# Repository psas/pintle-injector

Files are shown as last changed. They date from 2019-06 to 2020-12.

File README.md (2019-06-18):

# Background

The Portland State Aerospace Society (PSAS) is seeking to launch a liquid bi-propellant rocket to a height of 100 km. One of the principal challenges in this endeavor is the development and testing of the rocket engine and associated subsystems. 

PSAS chose to develop a smaller scale, 2.2kN test engine prior to attempting a 100 km capable design. This is in keeping with PSAS’s technology development philosophy of iterative design where initial designs are built, tested, broken, and iterated towards fully functional and flight ready designs. 

The 2.2kN engine was designed to employ a liquid oxygen (LOX) centered pintle. In this design, LOX flows through the center of the pintle and is sprayed outward in a radial pattern. The fuel enters a chamber surrounding the base of the pintle and flows into the engine through the annular gap between the outer diameter of the pintle and the engine. (See Figures 1 & 2) Inside of the combustion chamber, the two propellants impinge upon each other at right angles. This, ideally, results in a cone shaped spray of well mixed fuel and oxidizer. 
 
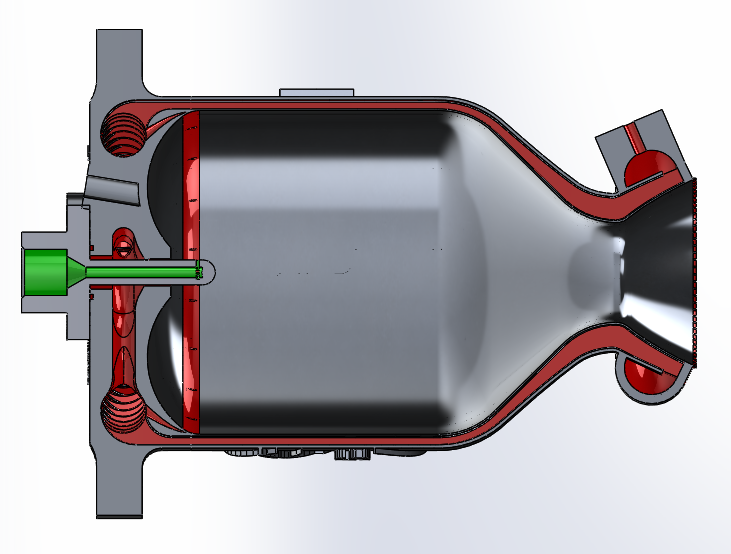
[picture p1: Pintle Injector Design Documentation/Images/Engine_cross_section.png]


>Figure 1: Cross section of 2.2 kN engine. Fuel flow path shown in red, LOX flow path shown in green.

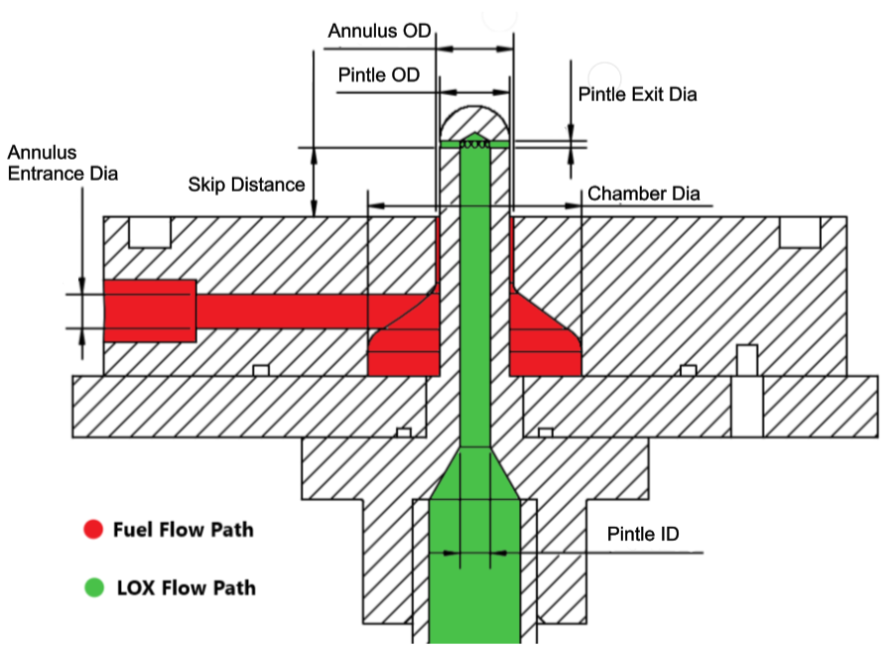
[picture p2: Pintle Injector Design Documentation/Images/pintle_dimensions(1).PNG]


> Figure 2: cross section view of genaric pintle V1 & V2 geometry.

The choice to use this style of injector was finalized by the 2015-2016 capstone team who designed the 2.2kN engine. The use of a pintle type injector is not specifically required for this size of engine. That stated, the initial 2.2kN engine was designed specifically to work with a pintle type injector, which locked a number of the design parameters which may have otherwise been available. The most noteworthy restrictions imposed are that the injector can only be LOX centered, and has a maximum envelope for the outer diameter of the annular gap.

# Theory and Design 

An instructional document was created while developing the injector for our first engine that attempts to distill the fundamental theory, design parameters, and the lessons learned from this project.

# V Series Injector

The first pintle injector design developed is the V series.

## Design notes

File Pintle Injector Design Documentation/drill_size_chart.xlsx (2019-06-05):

Size | Decimal Equivalent (in)
97 | 0.0059
96 | 0.0063
95 | 0.0067
94 | 0.0071
93 | 0.0075
92 | 0.0079
91 | 0.0083
90 | 0.0087
89 | 0.0091
88 | 0.0095
.25 mm | 0.0098
87 | 0.01
86 | 0.0105
85 | 0.011
84 | 0.0115
.30 mm | 0.0118
83 | 0.012
82 | 0.0125
.32 mm | 0.0126
81 | 0.013
80 | 0.0135
.35 mm | 0.0138
.36 mm | 0.0142
79 | 0.0145
.38 mm | 0.015
1/64" | 0.0156
.40 mm | 0.0157
78 | 0.016
.42 mm | 0.0165
.44 mm | 0.0173
.45 mm | 0.0177
77 | 0.018
.46 mm | 0.0181
.48 mm | 0.0189
.50 mm | 0.0197
76 | 0.02
75 | 0.021
.55 mm | 0.0217
74 | 0.0225
.60 mm | 0.0236
73 | 0.024
72 | 0.025
.65 mm | 0.0256
71 | 0.026
.70 mm | 0.0276
70 | 0.028
69 | 0.0292
.75 mm | 0.0295
68 | 0.031
1/32" | 0.0312
.80 mm | 0.0315
67 | 0.032
66 | 0.033
.85 mm | 0.0335
65 | 0.035
.90 mm | 0.0354
64 | 0.036
63 | 0.037
.95 mm | 0.0374
62 | 0.038
61 | 0.039
1.00 mm | 0.0394
60 | 0.04
59 | 0.041
1.05 mm | 0.0413
58 | 0.042
57 | 0.043
1.10 mm | 0.0433
1.15 mm | 0.0453
56 | 0.0465
3/64" | 0.0469
1.20 mm | 0.0472
1.25 mm | 0.0492
1.30 mm | 0.0512
55 | 0.052
1.35 mm | 0.0531
54 | 0.055
1.40 mm | 0.0551
1.45 mm | 0.0571
1.50 mm | 0.0591
53 | 0.0595
1.55 mm | 0.061
1/16" | 0.0625
1.60 mm | 0.063
52 | 0.0635
1.65 mm | 0.065
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

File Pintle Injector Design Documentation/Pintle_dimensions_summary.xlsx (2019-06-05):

Pintle Injector V1 |  |  | Pintle Injector V2
Pintle |  |  | Pintle
Flow Entrance dia. | 0.402 | in | Flow Entrance dia. | 0.402 | in
Inner Diameter | 0.12 | in | Inner Diameter | 0.221 | in
Orifice diameter | 0.03125 | in | Orifice diameter | 0.0595 | in
# of orifices | 12 | - | # of orifices | 12 | -
Wall Thickness | 0.0805 | in | Wall Thickness | 0.1 | in
Blockage Factor | 0.425 | - | Blockage Factor | 0.540 | -
Annulus |  |  | Annulus
Flow Entrance dia. | 0.136 | in | Flow Entrance dia. | 0.25 | in
# of Entrances | 1 | - | # of Entrances | 1 | -
Chamber radius | 0.4325 | in | Chamber radius | 0.4325 | in
Pintle OD | 0.281 | in | Pintle OD | 0.421 | in
Annulus Outer dia. | 0.3105 | in | Annulus Outer dia. | 0.4688 | in
Annular Gap | 0.01475 | in | Annular Gap | 0.0239 | in

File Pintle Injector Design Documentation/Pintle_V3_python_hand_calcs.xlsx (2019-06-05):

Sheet: Injector V3 mjp T4A
Pintle |  | values | units |  | Annulus |  | values | units
Entrance diameter |  | 0.44 | in |  | Entrance diameter |  | 0.25 | in
Inner Diameter |  | 0.221 | in |  | Channel Width |  | 0.25 | in
Outer Diameter |  | 0.421 | in |  | Channel Depth |  | 0.21 | in
Exit Diameter |  | 0.0635 | in |  | Chamber Diameter |  | 0.865 | in
Number of Orifices |  | 12 |  |  | Annulus Outer Diameter |  | 0.5156 | in
Blockage Factor |  | 0.576 |  |  | Annular Gap |  | 0.0473 | in
Pintle Version | Estimated Loss coef | Working Fluid | T intensity | T lenght Scale mm
MJP test 4 | 2.967 | water | 0.1225 | 4.247
Pintle Hand Calculations |  |  |  |  |  |  |  |  |  |  |  | Pintle CFD Results |  |  |  |  |  |  |  |  |  | Experimental Results
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

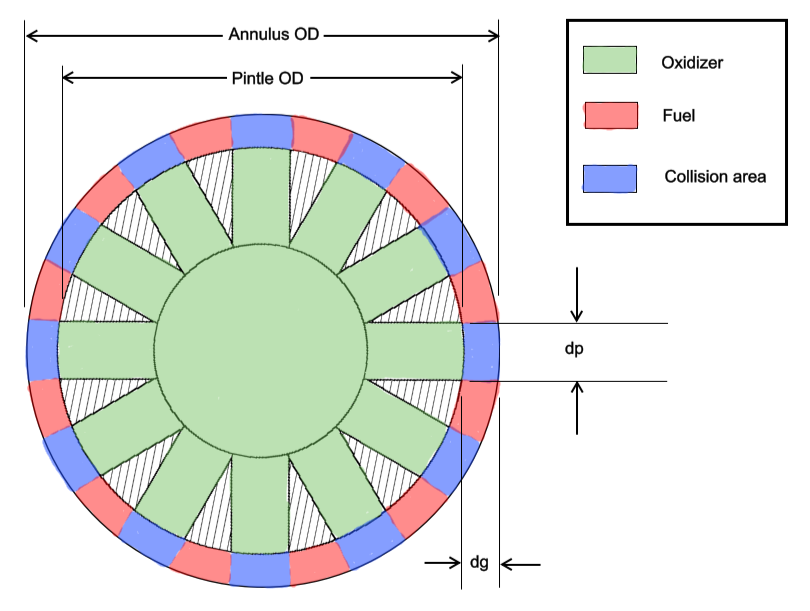
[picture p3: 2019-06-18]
Pintle Injector Design Documentation/Images/momentum_ratio_diagram.PNG

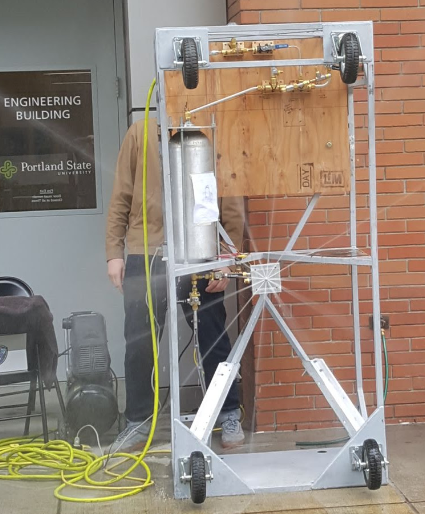
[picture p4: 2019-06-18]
Pintle Injector Design Documentation/Images/V2_radial_spray2.PNG

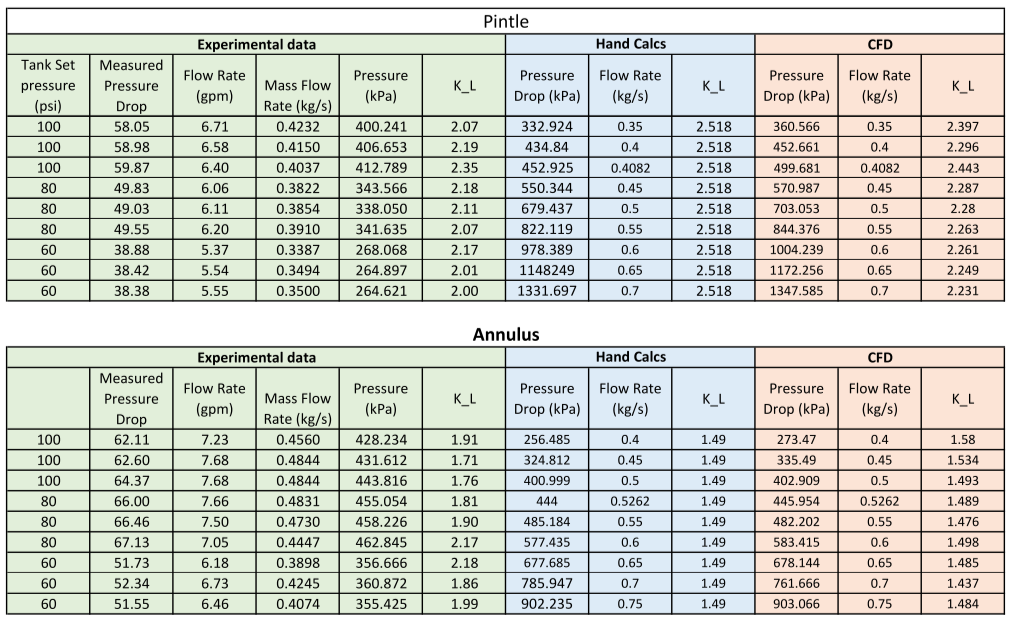
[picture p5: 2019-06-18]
Pintle Injector Design Documentation/Images/V2_data_summary.PNG

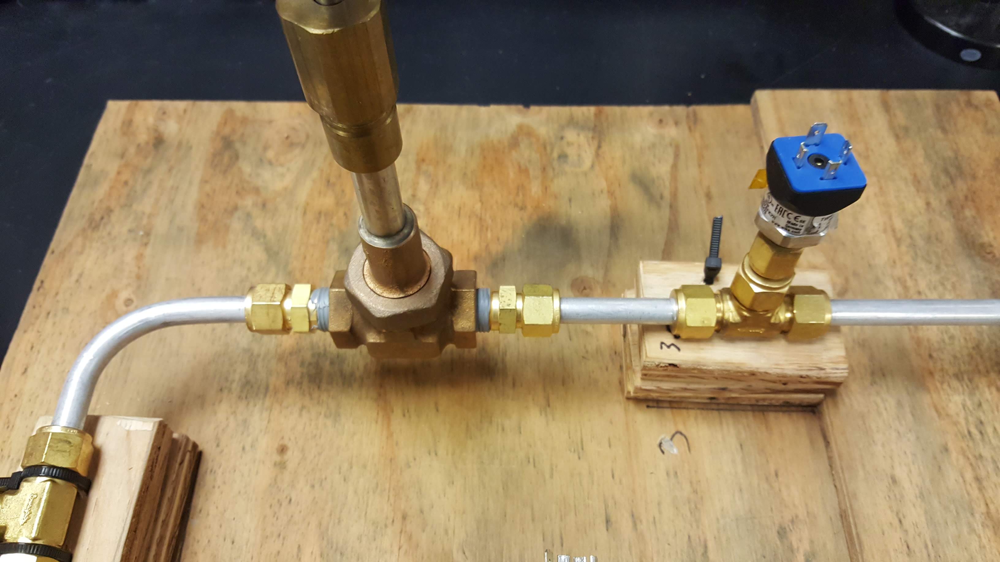
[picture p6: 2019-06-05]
Pintle Injector Design Documentation/Images/globe valve set up.jpg

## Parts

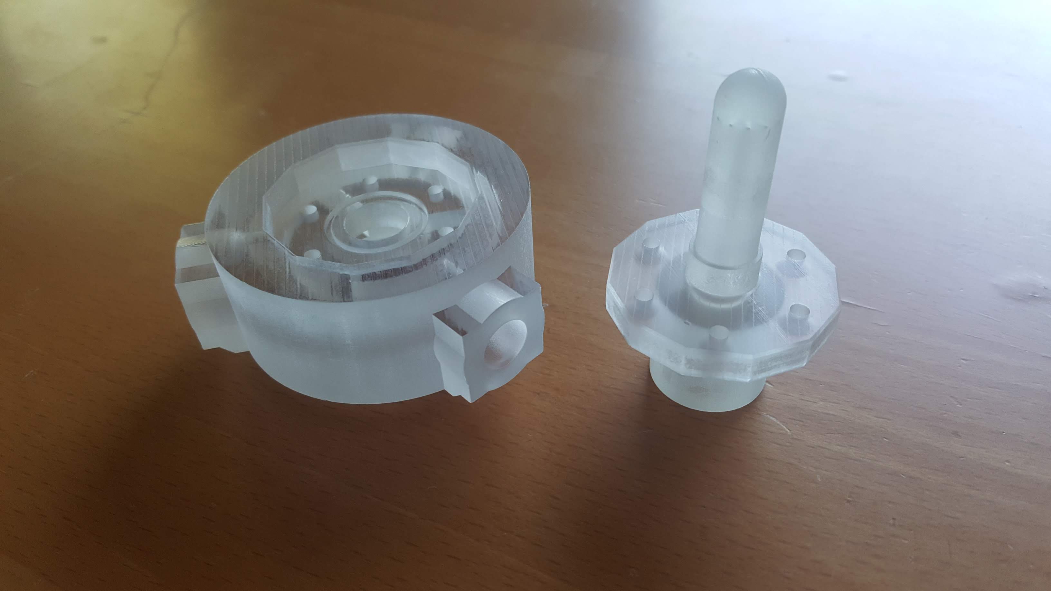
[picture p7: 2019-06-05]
V_Series/Images/V3_injector_parts.jpg

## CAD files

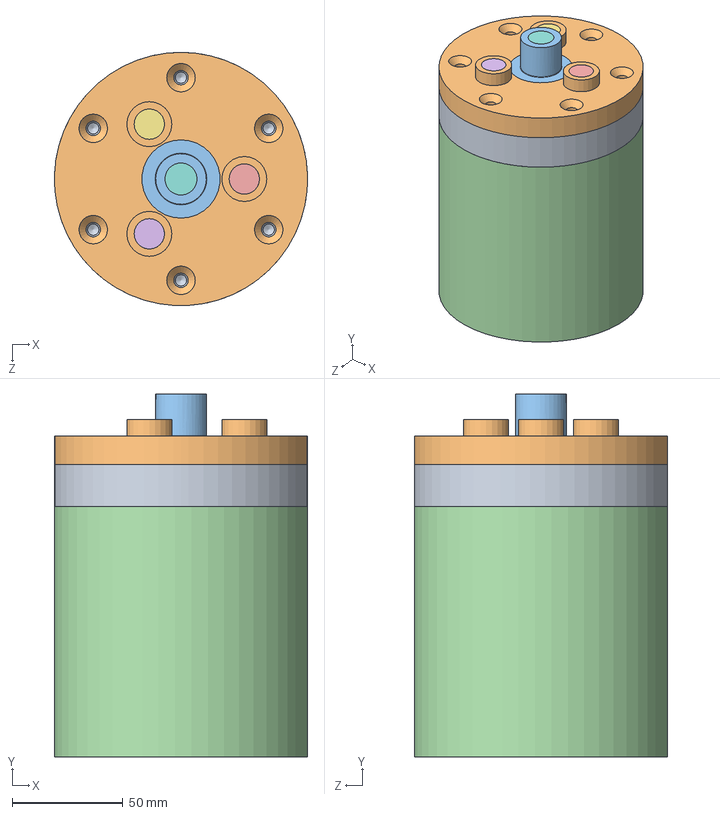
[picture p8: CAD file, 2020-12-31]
V_Series/Pintle_V3_CAD/Assembly_Pintle_V3.SLDASM
114.2 x 163.8 x 114.3 mm
Part_annulus_base_v3
Part_V3_Top_Plate
Part_V3_Pintle
Outlet_Lid_For_Sim
LID1
LID2
LID3
LID4

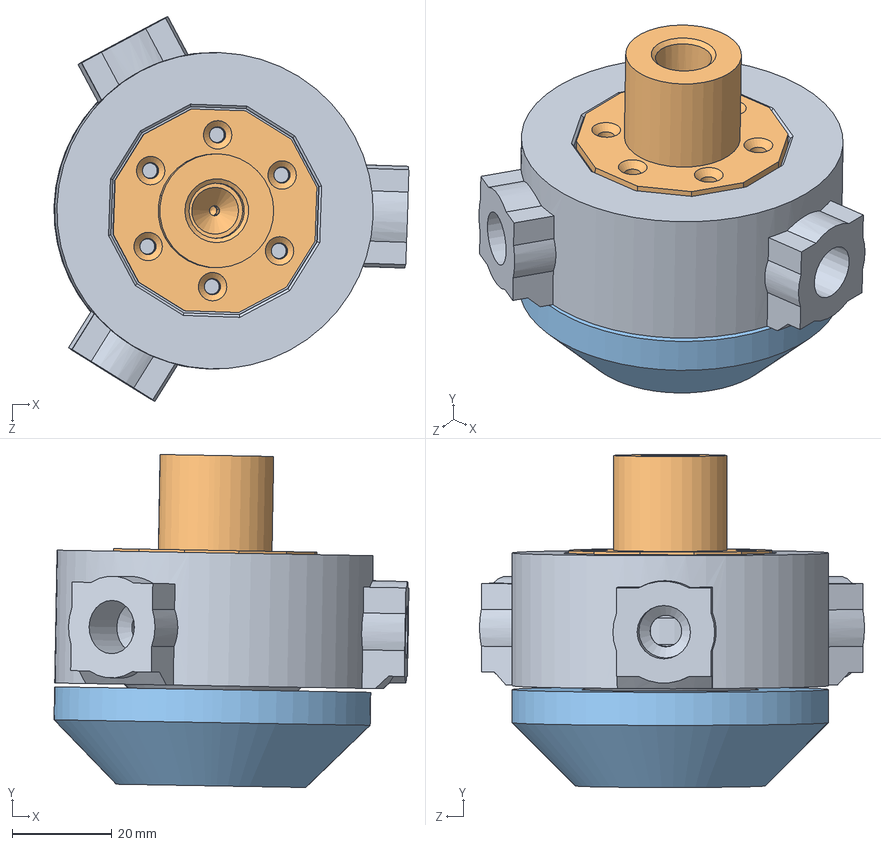
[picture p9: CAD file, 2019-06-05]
V_Series/Pintle_V3_CAD/Assembly_Pintle_V3_MJP.SLDASM
71.2 x 66.8 x 77.3 mm
Part_annulus_base_v3_mjp
Part_V3_Pintle_MJP
Part_mjp_support

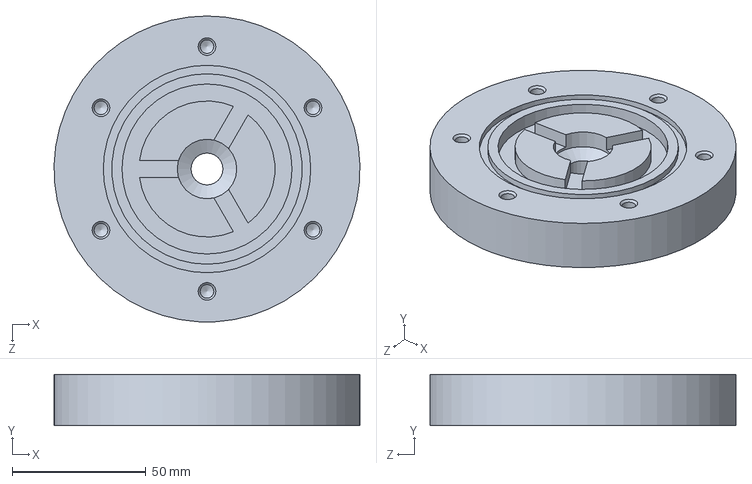
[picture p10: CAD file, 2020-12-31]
V_Series/Pintle_V3_CAD/Part_annulus_base_v3.SLDPRT
114.2 x 19.1 x 114.3 mm

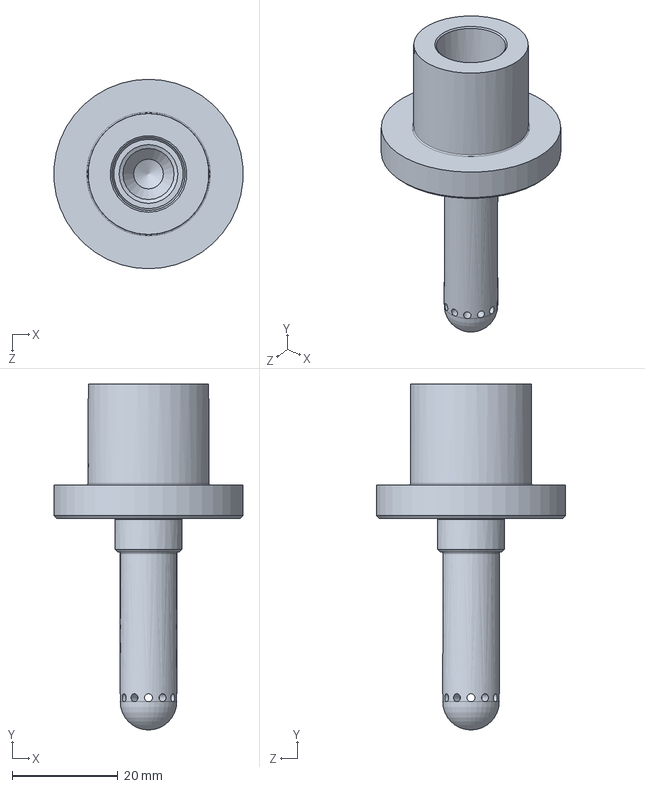
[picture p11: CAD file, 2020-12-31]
V_Series/Pintle_V3_CAD/Part_V3_Pintle.SLDPRT
35.7 x 65.4 x 35.8 mm

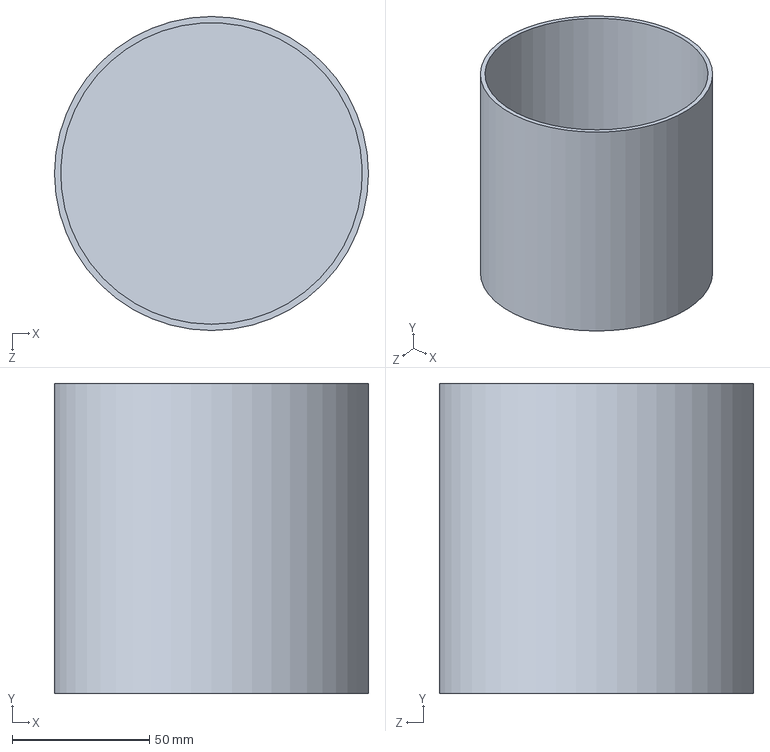
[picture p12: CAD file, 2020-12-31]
V_Series/Pintle_V3_CAD/Outlet_Lid_For_Sim.SLDPRT
114.3 x 113.0 x 114.3 mm

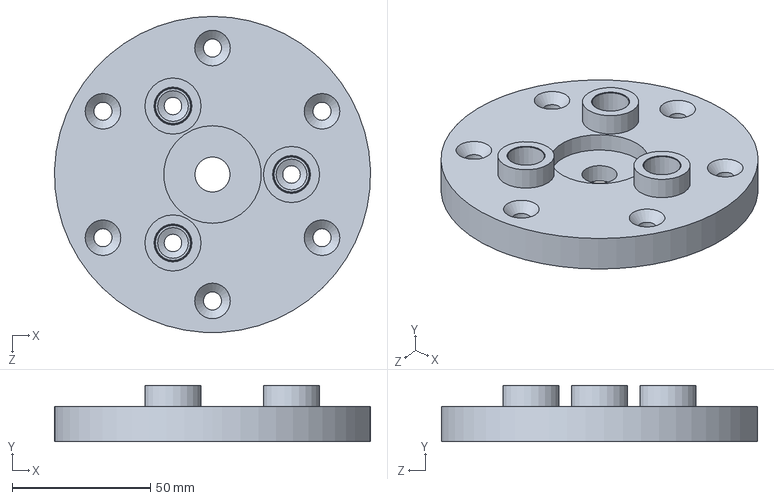
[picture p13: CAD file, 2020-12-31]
V_Series/Pintle_V3_CAD/Part_V3_Top_Plate.SLDPRT
114.2 x 20.3 x 114.3 mm

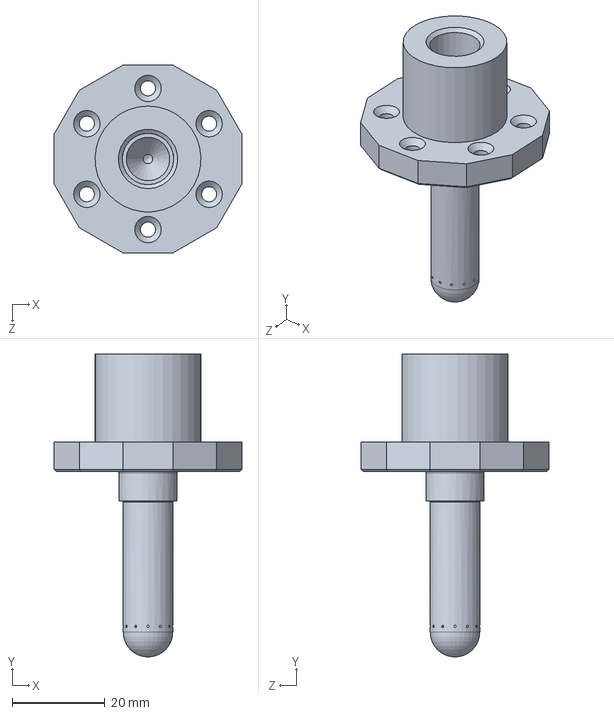
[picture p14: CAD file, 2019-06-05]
V_Series/Pintle_V3_CAD/Part_V3_Pintle_MJP.SLDPRT
40.5 x 65.4 x 40.5 mm

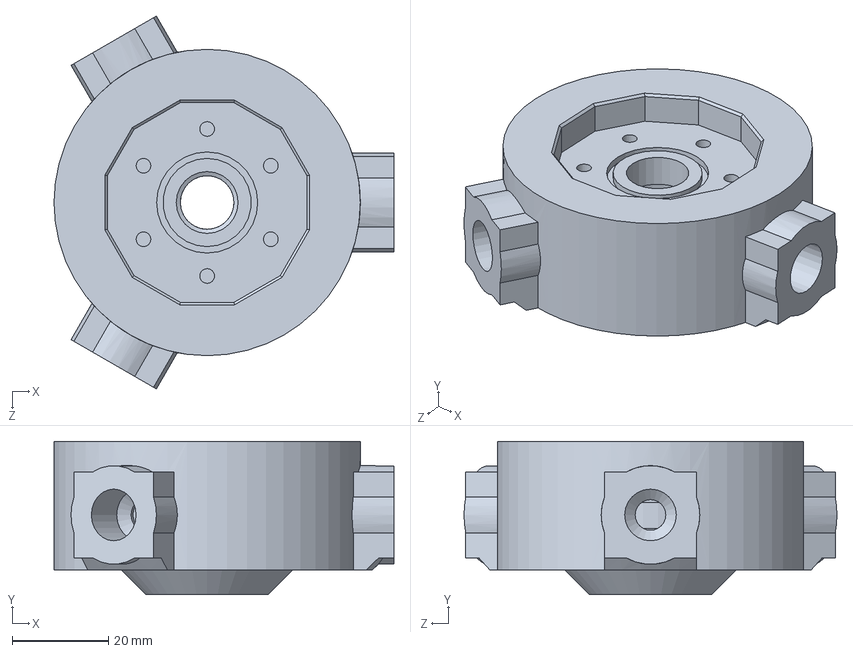
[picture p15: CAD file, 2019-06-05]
V_Series/Pintle_V3_CAD/Part_annulus_base_v3_mjp.SLDPRT
70.5 x 31.8 x 77.3 mm

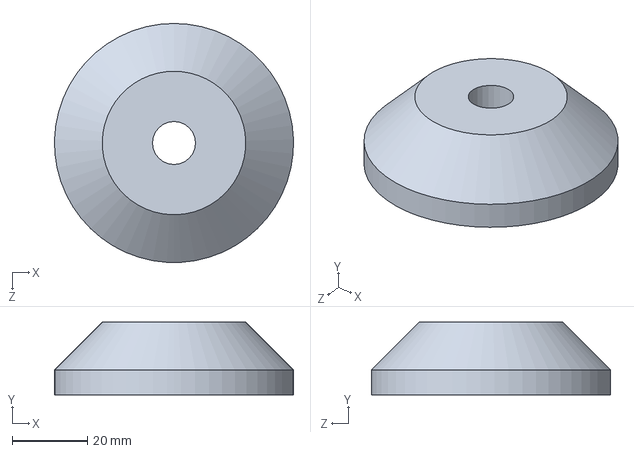
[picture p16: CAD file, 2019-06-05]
V_Series/Pintle_V3_CAD/Part_mjp_support.SLDPRT
63.5 x 19.3 x 63.5 mm

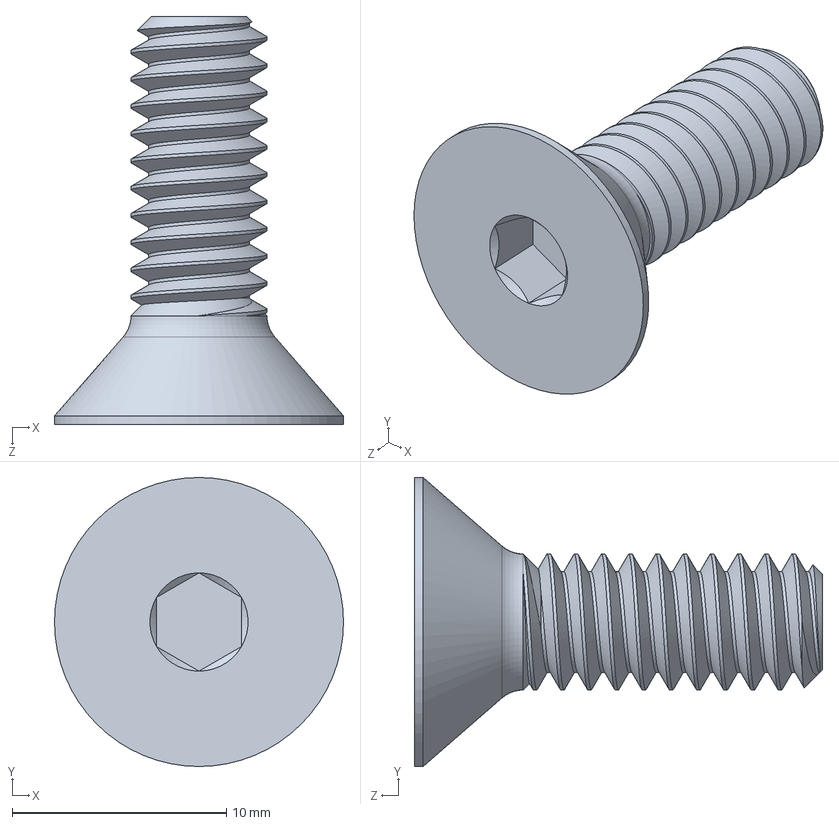
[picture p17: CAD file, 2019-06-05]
V_Series/Pintle_V3_CAD/90585A540_TYPE 316 SS FLAT-HEAD SOCKET CAP SCREW.SLDPRT
13.5 x 13.5 x 19.1 mm

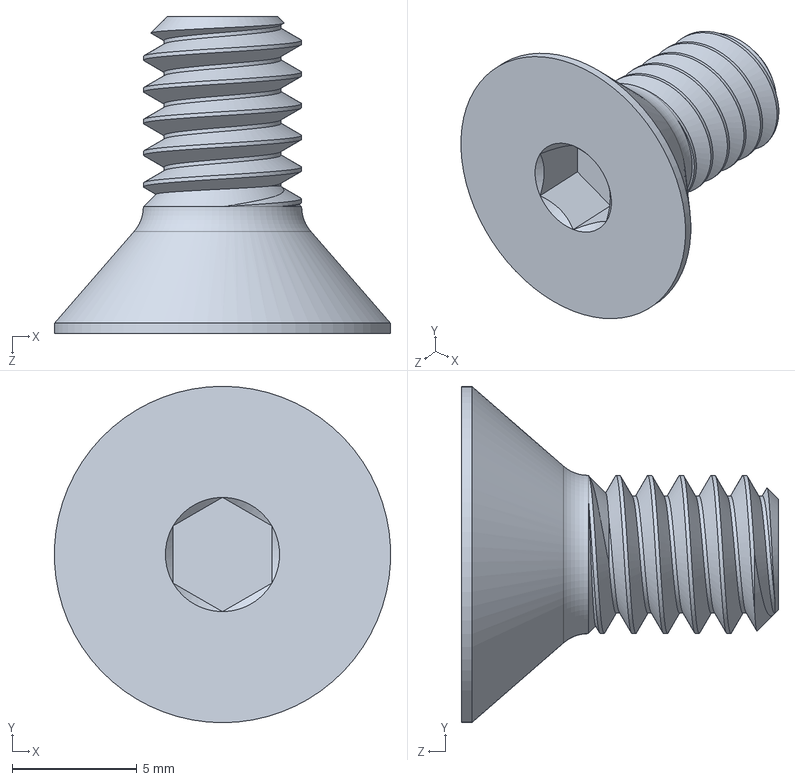
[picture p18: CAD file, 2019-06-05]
V_Series/Pintle_V3_CAD/90585A537_TYPE 316 SS FLAT-HEAD SOCKET CAP SCREW (1).SLDPRT
13.5 x 13.5 x 12.7 mm

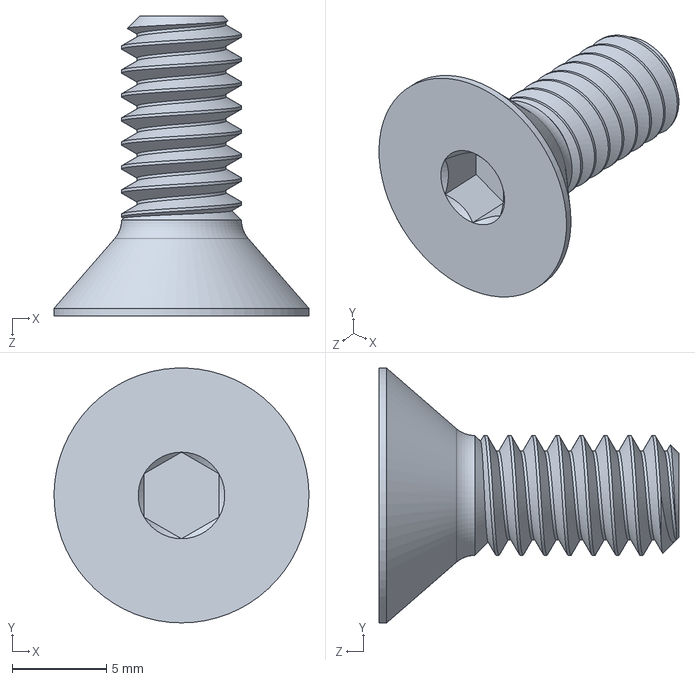
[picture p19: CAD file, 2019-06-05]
V_Series/Pintle_V3_CAD/90585A358_TYPE 316 SS FLAT-HEAD SOCKET CAP SCREW.SLDPRT
13.5 x 13.5 x 15.9 mm

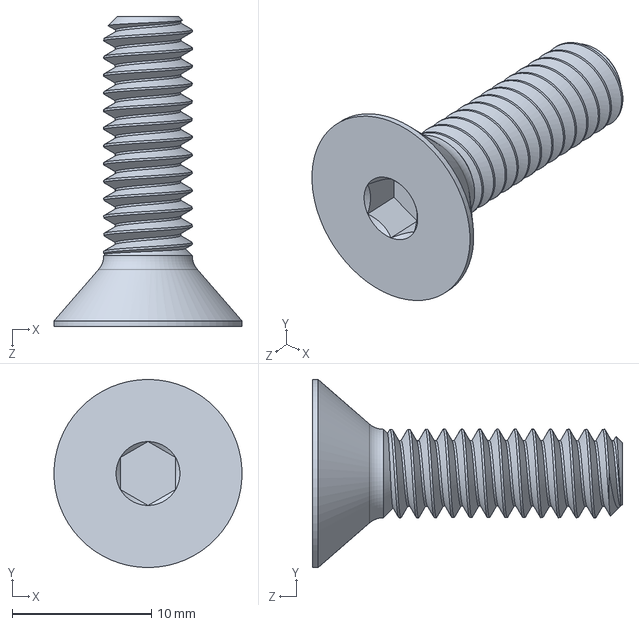
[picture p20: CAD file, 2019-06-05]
V_Series/Pintle_V3_CAD/90585A541_TYPE 316 SS FLAT-HEAD SOCKET CAP SCREW.SLDPRT
13.5 x 13.5 x 22.2 mm

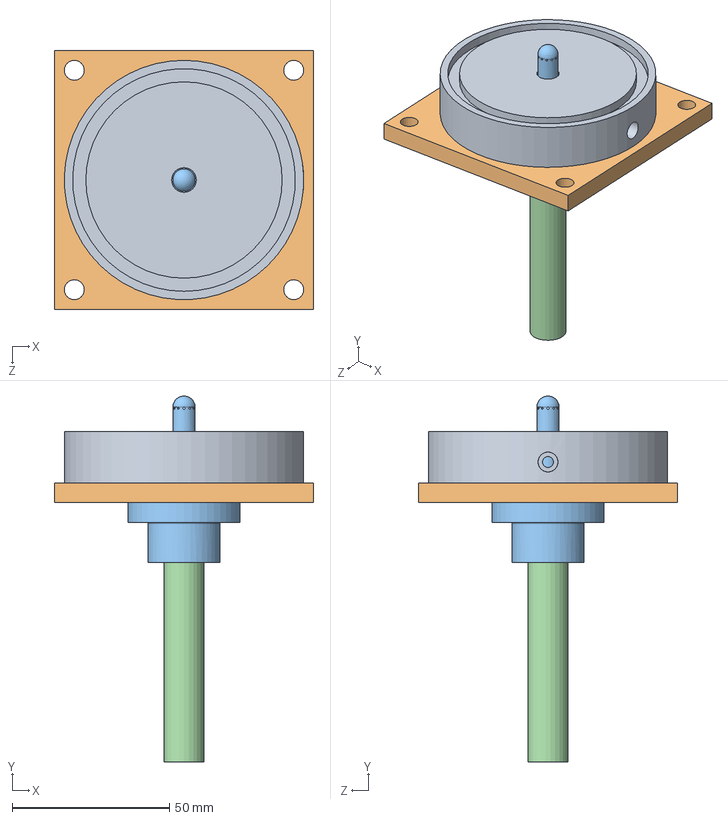
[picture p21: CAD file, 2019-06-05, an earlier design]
V_Series/Pintle_V1_CAD/Assembly_Cold_Test.SLDASM
82.5 x 116.5 x 82.5 mm
Part_Cold_Test_Annulus_V1
Part_Cold_Test_Plate_V1
Part_Pintle_V1
Part_SSTube

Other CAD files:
V_Series/Pintle_V3_CAD/LID1.SLDPRT
V_Series/Pintle_V3_CAD/LID4.SLDPRT
V_Series/Pintle_V3_CAD/LID2.SLDPRT
V_Series/Pintle_V3_CAD/LID3.SLDPRT
V_Series/Pintle_V1_CAD/Assembly_Cold_Test dimensions.SLDDRW
V_Series/Pintle_V1_CAD/Part_Cold_Test_Annulus_V1.SLDPRT
V_Series/Pintle_V1_CAD/Part_Cold_Test_Plate_V1.SLDPRT
V_Series/Pintle_V1_CAD/Part_Pintle_V1.SLDPRT
V_Series/Pintle_V1_CAD/Part_Pintle_V2.2.SLDPRT
V_Series/Pintle_V1_CAD/Part_SSTube.SLDPRT
V_Series/Pintle_V1_CAD/test.SLDASM
V_Series/Pintle_V2_CAD/Assembly_Jig_V2.SLDASM
V_Series/Pintle_V2_CAD/Assembly_V2_Cold_Test.SLDASM
V_Series/Pintle_V2_CAD/Drawing_V2_Cold_Test_Annulus_rough.SLDDRW
V_Series/Pintle_V2_CAD/Drawing_V2_Cold_Test_Plate_rough.SLDDRW
V_Series/Pintle_V2_CAD/Drawing_V2_Pintle_rough.SLDDRW
V_Series/Pintle_V2_CAD/Part_SSTube.SLDPRT
V_Series/Pintle_V2_CAD/Part_V1_Pintle.SLDPRT
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

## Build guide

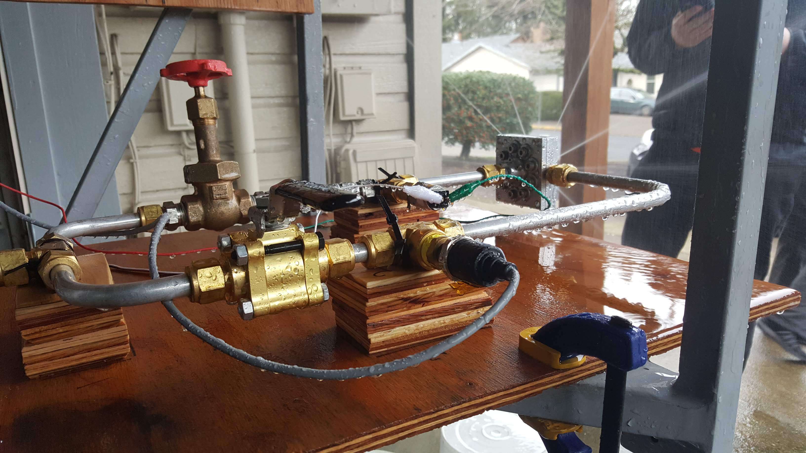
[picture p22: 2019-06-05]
V_Series/Images/Initial setup.jpg

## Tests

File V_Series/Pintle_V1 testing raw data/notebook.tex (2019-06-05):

% Default to the notebook output style

% Inherit from the specified cell style.

\documentclass[11pt]{article}

    \usepackage[T1]{fontenc}
    % Nicer default font (+ math font) than Computer Modern for most use cases
    \usepackage{mathpazo}

    % Basic figure setup, for now with no caption control since it's done
    % automatically by Pandoc (which extracts ![](path) syntax from Markdown).
    \usepackage{graphicx}
    % We will generate all images so they have a width \maxwidth. This means
    % that they will get their normal width if they fit onto the page, but
    % are scaled down if they would overflow the margins.
    \makeatletter
    \def\maxwidth{\ifdim\Gin@nat@width>\linewidth\linewidth
    \else\Gin@nat@width\fi}
    \makeatother
    \let\Oldincludegraphics\includegraphics
    % Set max figure width to be 80% of text width, for now hardcoded.
    \renewcommand{\includegraphics}[1]{\Oldincludegraphics[width=.8\maxwidth]{#1}}
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
\expandafter\def\csname PY@tok@kc\endcsname{\let\PY@bf=\textbf\def\PY@tc##1{\textcolor[rgb]{0.00,0.50,0.00}{##1}}}
\expandafter\def\csname PY@tok@kd\endcsname{\let\PY@bf=\textbf\def\PY@tc##1{\textcolor[rgb]{0.00,0.50,0.00}{##1}}}
\expandafter\def\csname PY@tok@kn\endcsname{\let\PY@bf=\textbf\def\PY@tc##1{\textcolor[rgb]{0.00,0.50,0.00}{##1}}}
\expandafter\def\csname PY@tok@kr\endcsname{\let\PY@bf=\textbf\def\PY@tc##1{\textcolor[rgb]{0.00,0.50,0.00}{##1}}}
\expandafter\def\csname PY@tok@bp\endcsname{\def\PY@tc##1{\textcolor[rgb]{0.00,0.50,0.00}{##1}}}
\expandafter\def\csname PY@tok@fm\endcsname{\def\PY@tc##1{\textcolor[rgb]{0.00,0.00,1.00}{##1}}}
\expandafter\def\csname PY@tok@vc\endcsname{\def\PY@tc##1{\textcolor[rgb]{0.10,0.09,0.49}{##1}}}
\expandafter\def\csname PY@tok@vg\endcsname{\def\PY@tc##1{\textcolor[rgb]{0.10,0.09,0.49}{##1}}}
\expandafter\def\csname PY@tok@vi\endcsname{\def\PY@tc##1{\textcolor[rgb]{0.10,0.09,0.49}{##1}}}
\expandafter\def\csname PY@tok@vm\endcsname{\def\PY@tc##1{\textcolor[rgb]{0.10,0.09,0.49}{##1}}}
\expandafter\def\csname PY@tok@sa\endcsname{\def\PY@tc##1{\textcolor[rgb]{0.73,0.13,0.13}{##1}}}
\expandafter\def\csname PY@tok@sb\endcsname{\def\PY@tc##1{\textcolor[rgb]{0.73,0.13,0.13}{##1}}}
\expandafter\def\csname PY@tok@sc\endcsname{\def\PY@tc##1{\textcolor[rgb]{0.73,0.13,0.13}{##1}}}
\expandafter\def\csname PY@tok@dl\endcsname{\def\PY@tc##1{\textcolor[rgb]{0.73,0.13,0.13}{##1}}}
\expandafter\def\csname PY@tok@s2\endcsname{\def\PY@tc##1{\textcolor[rgb]{0.73,0.13,0.13}{##1}}}
\expandafter\def\csname PY@tok@sh\endcsname{\def\PY@tc##1{\textcolor[rgb]{0.73,0.13,0.13}{##1}}}
\expandafter\def\csname PY@tok@s1\endcsname{\def\PY@tc##1{\textcolor[rgb]{0.73,0.13,0.13}{##1}}}
\expandafter\def\csname PY@tok@mb\endcsname{\def\PY@tc##1{\textcolor[rgb]{0.40,0.40,0.40}{##1}}}
\expandafter\def\csname PY@tok@mf\endcsname{\def\PY@tc##1{\textcolor[rgb]{0.40,0.40,0.40}{##1}}}
\expandafter\def\csname PY@tok@mh\endcsname{\def\PY@tc##1{\textcolor[rgb]{0.40,0.40,0.40}{##1}}}
\expandafter\def\csname PY@tok@mi\endcsname{\def\PY@tc##1{\textcolor[rgb]{0.40,0.40,0.40}{##1}}}
\expandafter\def\csname PY@tok@il\endcsname{\def\PY@tc##1{\textcolor[rgb]{0.40,0.40,0.40}{##1}}}
\expandafter\def\csname PY@tok@mo\endcsname{\def\PY@tc##1{\textcolor[rgb]{0.40,0.40,0.40}{##1}}}
\expandafter\def\csname PY@tok@ch\endcsname{\let\PY@it=\textit\def\PY@tc##1{\textcolor[rgb]{0.25,0.50,0.50}{##1}}}
\expandafter\def\csname PY@tok@cm\endcsname{\let\PY@it=\textit\def\PY@tc##1{\textcolor[rgb]{0.25,0.50,0.50}{##1}}}
\expandafter\def\csname PY@tok@cpf\endcsname{\let\PY@it=\textit\def\PY@tc##1{\textcolor[rgb]{0.25,0.50,0.50}{##1}}}
\expandafter\def\csname PY@tok@c1\endcsname{\let\PY@it=\textit\def\PY@tc##1{\textcolor[rgb]{0.25,0.50,0.50}{##1}}}
\expandafter\def\csname PY@tok@cs\endcsname{\let\PY@it=\textit\def\PY@tc##1{\textcolor[rgb]{0.25,0.50,0.50}{##1}}}

\def\PYZbs{\char`\\}
\def\PYZus{\char`\_}
\def\PYZob{\char`\{}
\def\PYZcb{\char`\}}
\def\PYZca{\char`\^}
\def\PYZam{\char`\&}
\def\PYZlt{\char`\<}
\def\PYZgt{\char`\>}
\def\PYZsh{\char`\#}
\def\PYZpc{\char`\%}
\def\PYZdl{\char`\$}
\def\PYZhy{\char`\-}
\def\PYZsq{\char`\'}
\def\PYZdq{\char`\"}
\def\PYZti{\char`\~}
% for compatibility with earlier versions
\def\PYZat{@}
\def\PYZlb{[}
\def\PYZrb{]}
\makeatother

    % Exact colors from NB
    \definecolor{incolor}{rgb}{0.0, 0.0, 0.5}
    \definecolor{outcolor}{rgb}{0.545, 0.0, 0.0}

    % Prevent overflowing lines due to hard-to-break entities
    \sloppy 
    % Setup hyperref package
    \hypersetup{
      breaklinks=true,  % so long urls are correctly broken across lines
      colorlinks=true,
      urlcolor=urlcolor,
      linkcolor=linkcolor,
      citecolor=citecolor,
      }
    % Slightly bigger margins than the latex defaults
    
    \geometry{verbose,tmargin=1in,bmargin=1in,lmargin=1in,rmargin=1in}

    \begin{document}

    \maketitle

    \section{Pintle V1 Test for 2.2kN Liquid Propellant Rocket
Engine}\label{pintle-v1-test-for-2.2kn-liquid-propellant-rocket-engine}

Dates of testing: 1/19/19, 1/26/19 \& 2/3/19

    \section{Introduction}\label{introduction}

The Portland State Aerospace Society is in the process of testing its
\(2.2kN\) (\(500 lb_f\)) regeneratively cooled bi-propellant rocket
motor. One of the critical steps prior to hot firing the motor is the
testing and validating of the propellant injector. For this motor, a
pintle style injector was selected and an aluminum test article was
machined according to the designs provided by the 2015 Capstone team.

    \section{Pintle Design:}\label{pintle-design}

The engine was designed to employ a liquid oxygen (LOX) centered pintle
design. In this design, LOX flows throu the center of the pintle and is
sprayed outward in a radial pattern. The fuel enters a chamber
surrounding the base of the pintle and enters the engine through the
annular gap between the outer radius of the pintle and the engine. (See
Figures 1 \& 2) Inside of the combustion chamber, the two propellants
impinge upon eachother at right angles. This, ideally, results in a cone
shaped spray of well mixed fuel and oxidizer.

\begin{quote}
Figure 1: Cross section of 2.2 kN engine. Fuel flow path shown in red,
LOX flow path shown in green.
\end{quote}

\begin{quote}
Figure 2: Cross section of Pintle with basic dimensions for flow paths.
\end{quote}

\subsection{Relevant Design
Requirements:}\label{relevant-design-requirements}

The pintle injector needs to meet the following requirements:

\begin{enumerate}
\def\labelenumi{\arabic{enumi}.}
\tightlist
\item
  Oxidizer: Liquid Oxygen (LOX)
\item
  Fuel: 70\% Isoproply Alchohol (IPA), 30\% water
\item
  Meet mass flow rates at a pressure differential between 15-20 \% of
  chamber pressure:

  \begin{itemize}
  \tightlist
  \item
    Engine chamber pressure 350 psi (as designed)
  \item
    Target pressure differential: 53-70 psi\\
  \end{itemize}
\item
  LOX mass flow rate of 0.9 lbm/s (0.4082 kg/s)
\item
  Fuel mass flow rate of 1.16 lbm/s (0.5262 kg/s)
\end{enumerate}

    \section{Objectives}\label{objectives}

Desired data and outcomes:

\begin{itemize}
\tightlist
\item
  Determine loss coefficients (\(C_L\))

  \begin{itemize}
  \tightlist
  \item
    Pintle (LOX path)
  \item
    Annulus (Fuel path)
  \end{itemize}
\item
  Verify desired flow rates acheived at a delta pressure of 70 psi
\end{itemize}

    \section{Equations and Theory}\label{equations-and-theory}

The first testing objective was to determine the loss coefficients for
the Pintle and Annulus flow paths. For practical, cost, and safety
reasons the initial testing was performed using water.

Flow coefficient for the style of orifice plate used in testing {[}1{]};

\begin{equation}
C_v = \frac{Q_{gpm}}{\sqrt{\Delta P}}
\label{eq1}
\tag{1}
\end{equation}

Where;

\$C\_v = \$ the flow coefficient

\(Q_{gpm} =\) is the volumentric flow rate in gallons per minute

\$\Delta P = \$ is the difference in pressure across the orifice

\$ \textbackslash{} \$

Mass flow rate:

\begin{equation}
 \dot{m} = \rho VA
\label{eq2}
\tag{2}
\end{equation}

Energy Equation, with elevation, velocity, and head loss due to friction
neglected:

\begin{equation}
P_1  = P_2 + C_L\frac{\rho V_2^2}{2}
\label{eq3}
\tag{3}
\end{equation}

Combining equation \ref{eq2} and \ref{eq3} by substituting
\(V = \frac{\dot{m}}{\rho A}\) and rearranging gives

\begin{equation}
\dot{m} = C_LA \sqrt{2\rho(\Delta P)}
\label{eq4}
\tag{4}
\end{equation}

Where;

\$C\_L = \$ Loss coefficients for Pintle and Annulus: (to be calculated)

\(A =\) Flow area(s) of Pintle/Annulus

\(\dot{m} =\) Mass Flow Rate (from flow meter)

\(\Delta P =\) Pressure upstream of Pintle/Annulus (gauge) - atmospheric
pressure (0 psi)

\$\rho = \$ Density of water (calculate based on temperature)

Note: Each flow path has multiple changes to flow area between point of
measurement and the atmosphere. As a result, it is being assumed
(possibly incorrectly) that the \(C_L\) and discharge area \(A\) are
coupled and the loss coefficient should incorporate both with the
understanding that the coefficient is only good for this specific
version of the pintle design;

\begin{equation}
C_LA = C_A = \frac{\dot{m}}{\sqrt{2\rho(\Delta P)}}
\label{eq5}
\tag{5}
\end{equation}

From this it was determined that in order to solve for \(C_A\) the
experimental set up needed to determine the mass flow rate and pressure
drop.

    \section{Methods}\label{methods}

The following test set up was designed to obtain the mass flow and
pressure measurements.

\begin{quote}
Figure 3: Schematic of Pintle Test Layout
\end{quote}

\subsection{Calibration:}\label{calibration}

\textbf{Pressure Transducers:}

The 5 pressure transducers were calibrated simultaneously on the stand
using compressed air for measurements at 0, 25, 50, 75, and 100 PSIG.
The system pressure was set using a bourdon tube style pressure gauge.
This calibration was repeated at the start of each day of testing.

\textbf{Flow measuremnt:}

Our initial test set up included a turbine flow meter (not shown in
schematic) located between the manual linear globe valve and pressure
transducer 2. This flow meter was found to be malfunctioning. We decided
to move forward with the test using only the calibrated orifice plate to
determine the total mass flow rate for the pintle and annulus.\\
The orifice was calibrated using multiple input pressures. The flow rate
was determined using a stop watch and a graduated container. Timing for
each of the tests began at the \(1/2\) gallon mark and ended at the 3.5
gallon mark in order allow the flow to reach a steady flow condition.
Times were recorded every quarter gallon and then plotted to determine
flow rates. Each of the flow rates was then plotted against the
corresponding pressure drop and compared to the average \(C_v\)
calculated from the experiment.

\begin{quote}
Figure 4: Flow rate curve and experimental flow rate data for calibrated
orifice. Experimental data indicated that the accuracy of the orifice
drops off steeply at pressure differences over 30 psi. More on this in
the Issues section
\end{quote}

After determining the \(C_v\) of the main orifice, the pintle test
article was attached to the system and the following test proceedure was
followed:

    \section{Test procedure.}\label{test-procedure.}

\begin{enumerate}
\def\labelenumi{\arabic{enumi}.}
\item
  With valve to fuel circuit closed and valve to LOX circuit open. Test
  LOX circuit at tank pressures of 50, 100, and 200 psi\(^\dagger\). Use
  flow rate data from orifice plate and pressure recorded above the
  pintle to determine loss coefficient for pintle flow path,
  \(C_{A,pintle}\).
\item
  With valve to LOX circuit closed and valve to Fuel circuit open. Test
  fuel circuit at tank pressures of 50, 100, and 200 psi\(^\dagger\).
  Use flow rate data from orifice plate and pressure recorded above the
  annulus to determine loss coefficient for annulus flow path,
  \(C_{A,annulus}\).
\item
  Starting with Fuel circuit valve open, and LOX circuit valve closed,
  adjust flow through pintle using LOX circuit glove valve unitl a
  45\(^{\circ}\) spray is observed. Spray angle to be measured visually
  using a large laser cut protractor with radial spokes every
  15\(^{\circ}\).
\item
  With spray angle adjusted to 45\(^{\circ}\), record total flow rate
  using orifice plate. Determine LOX circuit and Fuel Circuit flow rates
  using previously calculated loss coefficients, \(C_{A,pintle}\) and
  \(C_{A,annulus}\) to determine the flow rates for each fluid circuit.
  Double
\item
  Repeat steps 3 and 4 at 50, 100, and 200 psi.
\item
  After testing, check flow rates for each circuit against the
  continuity equation: \[Q_{total} = Q_{pintle}+Q_{annulus} \]
\end{enumerate}

\$ \textbackslash{} \$

\begin{quote}
\(\dagger\) Tank pressures used for each day of testing. - 1/19: 50,
100, and 200 PSI, Nitrogen was used for the 200 PSI test. - 1/26: 25,
50, 75, 100 PSI - 2/3: 100 PSI only
\end{quote}

    \section{Known Issues with experimental set
up}\label{known-issues-with-experimental-set-up}

A number of issues were encountered during testing which potentially
invalidate some of the collected data. These are being written up as
lessons learned for future testing.

\subsection{Damaged turbine flow
meter}\label{damaged-turbine-flow-meter}

When inspected, it was determined that debris had gotten into the flow
meter and damaged the turbine. Root cause is believed to be mis-use due
to lack of adequate documentation on proper use, maintainence, and
storage the flow meter. The turbine flow meter was located just
downstream of the globe valve for the tests performed on 1/19 and was
removed prior to the the tests performed on 1/26.\\
- Recommendation for when a new flow meter is purchased, or otherwise
obtained; both the flow meter and a summery write up of how to use,
calibrate, and maintain the flow meter be bagged in a labeled container.
Any team which desires to use the flow meter must first review the
instructions and is responsible for following them.

\subsection{Orifice flow meter set up}\label{orifice-flow-meter-set-up}

The first issue with our orifice plate set up was that we had difficulty
locating an orfice plate which could measure the flow rates we require
in a 0.5 inch tube. The closest found was from
\href{http://catalog.okeefecontrols.com/item/precision-metal-orifices-npt-connections/precision-metal-orifices-npt-adapter/h-125-br}{O'Keefe
Controls} with a flow rate of 3.096 gpm of water at 70 psi. This orific
was modified based on sizing calculations provided by the manufaturer
with the intention to test the orifice across the expected flow ranges
to determine the correct orifice \(C_v\).

The second, larger, issue is in where the pressure tranducers were
located relative to the orifice. The pressure transducers were placed as
close to the orifice plate as our fittings would allow, rather than at
one of the standard distances called out in various flow measurement
references. At the time the orifice meter was constructed it was
believed that we could compensate for the placement of the pressure
transducers via calibration.

\begin{quote}
Figure 5: Orifice and pressure transducer set up used for experiment.
Downstream pressure transducer (PT \#3) is approximately 5.5 tube
diameters downstream of orifice.
\end{quote}

For the initial calibration tests without the pintle, this appeared to
be sufficient. However, when pintle was attached, we were not able to
detect a pressure drop across the orifice plate when testing the LOX
circuit.

\begin{quote}
Figure 6: Pressure readings for LOX circuit flow only. Pressure drop
across the orifice was not detectable with testing set up used. From the
data, we were not able to determine the flow rate of the water for the
series of tests performed on 1/26/19
\end{quote}

\subsection{Leaky gate valve}\label{leaky-gate-valve}

On the first day of testing it was noted that our manual globe valve was
not water tight. As we did not have a replacement on hand, we proceeded
with the tests with the understanding that there would be some water
flow and pressure loss through the LOX circuit when testing the Fuel
circuit. This valve was replaced prior to the testing performed on 1/26
with a properly functioning globe valve.

\subsection{Loose wire conncetion between DAQ and pressure
transducers}\label{loose-wire-conncetion-between-daq-and-pressure-transducers}

When calibrating our pressure transducers on 1/23, we found a loose wire
which was producing a high level of noise. Once properly secured our
pressure transducer readings became significanly less scattered. When
comparing the collected data between 1/19 and subsequent testing dates
it became obvious that the data collected from 1/19 was affected by
this, or a similar issue. This issue potentially also affected the
original orifice flow rate data (shown in Figure 4 above), which was not
realized until after testing was completed.

\subsection{Debris trapped in the
annulus}\label{debris-trapped-in-the-annulus}

On the first day of testing it was noted that the spray from the annulus
was uneven. When a \(45^{\circ}\) spray test was performed, we observed
poor mixing and atomization. Prior to the testing on 1/26 the pintle
test article was disassembled and fully cleaned. While cleaning some
metal chips were found trapped in the annulus (Figure 5). After this
debris was removed, we observed significant improvement in the mixing
and atomization (figure 6).

\begin{quote}
Figure 5: Debris found in annulus.
\end{quote}

\begin{quote}
Figure 6: Before and after images from spray angle testing, video can be
found
\href{https://github.com/psas/liquid-engine-test-stand/blob/master/Pintle/Pintle_V1\%20testing/Images/side\%20by\%20side\%20spray\%20angle.wmv}{here}.
\end{quote}

"Where accuracy is important, direct flow calibration is recommended.
Water flow calibration, using tap water, a stop watch, and a glass
graduate (or a pail and scale) to measure total flow, is readily carried
out in the instrument shop or laboratory. For viscous liquids,
calibration with the working fluid is preferable, because viscosity has
a substantial effect on most units. Calibration across the working range
is recommended, given that precise conformity to the square law may not
exist." - Instrument Engineers Handbook

    \section{Results}\label{results}

The pintle testing took place over the course of three weekends. A
summary of each days testing and the results are presented here, with
links at the bottom of this section to the raw data collected for each
day of testing.

\subsection{Day 1: 1/19/2019}\label{day-1-1192019}

As stated in the issues section, the calibration done on this date was
adversely affected by loose wiring. While we did obtain data, the the
spread and some of the pressure readings obtained raise questions about
its accuracy.

\href{https://github.com/psas/liquid-engine-test-stand/tree/master/analysis/Pintle_V1\%20testing/Pintle\%20Test\%2001-19-2019}{Raw
test data for 1/19/2019}

\subsection{Day 2: 1/26/2019}\label{day-2-1262019}

Some interesting data was collected on the second day, however due to a
combination of the

As noted in the issues section, the flow rate data from the orifice is
suspect. Unfortunately without knowing how to back out the mass flow
rates from our data, we were unable to determine if the Pintle achieved
the required flow rates.

As an aside, we did note some interesting pressure phenomena during the
testing. Figure 7 shows and example of results we obtained when we
varied the flow through the LOX circuit using the globe valve. At the
start of the test the globe valve was full closed and was fully opened
then closed over approximately 40 seconds. For the data shown, the
upstream tank pressure was set to 75 PSIG.

At approximagely 15 seconds the a hissing sound (consistent with
cavitation) was coming from the globe valve. The hissing ceased at
approximatly 25 seconds into the test.

A substantial pressure rise in the LOX circuit was observed in the 25,
50 and all three of the 75 PSI tests where this test was repeated.

Also noticed was that as the pressure increased in the LOX circuit, the
pressure read by pressure transducer 3 (located just downstream of the
orifice) also increased. This resulted in the differential pressure
recorded across the orifice going down as we increased the flow through
the LOX circuit. The recorded pressure differential became negative
during the same time period as the hissing sound was observed in the
valve.

\begin{quote}
Figure 5: Graph of spray angle test. Tank pressure was set to 100 PSIG
at at test start. The globe valve used to control the flow to LOX
circuit was changed from fully closed, to fully open and back again.
Valve controling flow to fuel circuit remained fully open for entire
test.
\end{quote}

Initial efforts were made to try and understand what caused the pressure
increase in the LOX circuit and several theories have been sugested. At
this time we have not pursued looking verifying these theories. It is
expected that a better testing set up with independant flow paths for
each working fluid will provide more accurate and usable flow data.

When running tests through only the LOX or Fuel circuits, unusual
pressure spikes were not observed, nor did we note any indications of
possible cavitation.

\href{https://github.com/psas/liquid-engine-test-stand/tree/master/analysis/Pintle_V1\%20testing/Pintle\%20Test\%2001-26-2019}{Raw
test data for 1/26/2019}

\subsection{Day 3: 2/3/2019}\label{day-3-232019}

The agenda for day 3 of testing was to test the pintle and annulus at a
pressure within the target range and measure the flow rate.

Only two pressure transducers were calibrated for these tests, one for
each flow path.

To measure the flow rate we altered our set up slightly so that the
water leaving the pintle/annulus could be captured in a graduated
bucket. Each of the test runs was videod to enable us to more accurately
determine the flow rates.

During the analysis the calculated flow rates were compared and it was
determined that neither the Pintle nor Annulus met the requirement.
Table 1 shows the average pressure measurements and flow rates along
with the test requirement.

\begin{quote}
Table 1: Flow rate results for Pintle testing. Tests show that the
current design of the pintle does not obtain the needed flow rates.
\end{quote}

\href{https://github.com/psas/liquid-engine-test-stand/tree/master/analysis/Pintle_V1\%20testing/Pintle\%20Test\%2002-03-2019}{Raw
test data for 2/3/2019}

    \section{Next Steps}\label{next-steps}

The pintle needs to be redesigned so that it acheives the required
propellant mass flow rates. In order to better understand the problem, a
new set of flow calculations were created using the asbuilt geometry for
comparision with the experimental results.

These calculations and the initial design work is taking place in a
separate notebook,
\href{https://github.com/psas/liquid-engine-test-stand/blob/master/Pintle/Pintle_V1\%20testing/01\%20Pintle\%20V1\%20Flow\%20Calculations\%20and\%20Analysis.ipynb}{01
Pintle V1 Flow Calculations and Analysis}.

    References:

{[}1{]} \href{Images/Orifice\%20Technical\%20Considerations.pdf}{O'keefe
Controls Technical Considerations Document}

    % Add a bibliography block to the postdoc

    \end{document}

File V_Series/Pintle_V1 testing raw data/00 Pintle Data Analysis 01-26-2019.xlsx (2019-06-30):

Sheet: Calculations
 | Pressure Calubration data from 01-26-2019
 |  | PT 1: Pintle Side | PT 2: LOX side | PT 3: orifice down | PT 4: orifice up | PT 5: Tank Pressure
 | slope | 10.37131397 | 3.500587365 | 5.31987896 | 5.870937915 | 1.060072804
 | intercept | 833.0608627 | 741.708571 | 747.6601 | 760.0710247 | 858.8483782
 | Flow rates from Main orifice bucket tests 01-19-2019
 | Pressures from Orifice pressure tests on 01-19-2019, average values used do not include transient pressure changes
 |  | Input (psig) | Avg. Flow Rate (gpm) | Avg. PT 4 (psi) | Avg. PT 3 (psi) | Average pressure drop (psi) | C_d value
 | Test 1 | 50 | 5.7465 | 27.58 | 21.958 | 5.622 | 2.423583518
 | Test 2 | 50 | 5.9926 | 29.047 | 22.925 | 6.122 | 2.421969263
 | Test 3 | 50 | 5.5805 | 31.591 | 24.819 | 6.772 | 2.144443645
 | Test 1 | 100 | 7.8441 | 56.252 | 44.645 | 11.607 | 2.302412473
 | Test 2 | 100 | 7.619 | 58.129 | 46.273 | 11.856 | 2.212732314
 | Test 3 | 100 | 8.0517 | 55.73 | 44.743 | 10.987 | 2.429114703
 | Test 1 | 200 | 11.69 | 124.401 | 98.444 | 25.957 | 2.294495776
Choked flow | Test 2 | 200 | 8.24 | 149.828 | 116.21 | 33.618 | 1.421154437
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

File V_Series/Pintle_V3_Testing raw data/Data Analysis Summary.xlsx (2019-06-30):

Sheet: FlowRate
 |  |  |  |  |  |  |  |  |  |  |  |  |  |  |  |  |  |  |  |  | Values used for other equations in spreadsheet
 |  |  |  |  |  |  |  |  |  |  |  |  |  |  |  |  |  |  |  |  | psi to pa | L to m3 | gal to m3 |  |  | Momentum Exit area |  |  |  | blockage factor
 |  |  | Liters | 0 | 2 | 3 | 4 | 5 | 6 | 7 | 8 | 9 | 10 | 11 | 12 | 13 |  |  |  |  | 0.000145 | 0.001 | 0.00378541 |  |  |  | single opening |  |  | 0.553
 |  |  | m^3 | 0 | 0.002 | 0.003 | 0.004 | 0.005 | 0.006 | 0.007 | 0.008 | 0.009 | 0.01 | 0.011 | 0.012 | 0.013 |  |  |  |  | density |  | exit area | m^2 |  | pintle | 1.8855e-06
 |  |  | kg (h20) | 0 | 1.999 | 2.999 | 3.999 | 4.998 | 5.998 | 6.998 | 7.998 | 8.997 | 9.997 | 10.997 | 11.996 | 12.996 |  |  |  |  | density h20 | 999.7 | Pintle | 2.2626e-05 |  |  | gap | pintle orifice dia | area
 |  |  | Gallons | 0 | 0.50 | 0.75 | 1.00 | 1.25 | 1.50 | 1.75 | 2.00 | 2.25 | 2.50 | 2.75 | 3.00 | 3.25 | 3.50 |  |  |  | density lox | 1141 | Annulus | 2.152788e-05 |  | annulus | 0.0006858 | 0.0015494 | 1.06257852e-06
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

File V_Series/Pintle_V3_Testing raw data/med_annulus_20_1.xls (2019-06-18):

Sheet: Analysis
timestamp | timer | pressure_1 | pressure_2 | pressure_2 | PT1 | PT2 | Transducer | Slope | Intercept
3:49:22 PM | 0.05 | 198 | 198 |  | 0.25 | 0 | 1 | 8 | 196
3:49:22 PM | 0.17 | 198 | 199 |  | 0.25 | 0.125 | 2 | 8 | 198
3:49:22 PM | 0.25 | 198 | 199 |  | 0.25 | 0.125
3:49:22 PM | 0.35 | 197 | 199 |  | 0.125 | 0.125 | Pintle Average
3:49:22 PM | 0.48 | 197 | 198 |  | 0.125 | 0 | 0.2673267327
3:49:22 PM | 0.55 | 198 | 199 |  | 0.25 | 0.125 | Annulus Average
3:49:22 PM | 0.65 | 198 | 199 |  | 0.25 | 0.125 | 16.10009225
3:49:23 PM | 0.80 | 197 | 199 |  | 0.125 | 0.125
3:49:23 PM | 0.85 | 198 | 199 |  | 0.25 | 0.125
3:49:23 PM | 0.95 | 198 | 200 |  | 0.25 | 0.25
3:49:23 PM | 1.05 | 198 | 199 |  | 0.25 | 0.125
3:49:23 PM | 1.15 | 198 | 200 |  | 0.25 | 0.25
3:49:23 PM | 1.25 | 197 | 199 |  | 0.125 | 0.125
3:49:23 PM | 1.35 | 197 | 199 |  | 0.125 | 0.125
3:49:23 PM | 1.45 | 197 | 199 |  | 0.125 | 0.125
3:49:23 PM | 1.55 | 197 | 199 |  | 0.125 | 0.125
3:49:23 PM | 1.65 | 198 | 199 |  | 0.25 | 0.125
3:49:23 PM | 1.75 | 197 | 199 |  | 0.125 | 0.125
3:49:24 PM | 1.85 | 197 | 199 |  | 0.125 | 0.125
3:49:24 PM | 1.95 | 198 | 198 |  | 0.25 | 0
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

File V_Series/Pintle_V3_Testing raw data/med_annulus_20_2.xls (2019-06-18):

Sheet: Analysis
timestamp | timer | pressure_1 | pressure_2 | pressure_2 | PT1 | PT2 | Transducer | Slope | Intercept
3:51:28 PM | 0.06 | 197 | 200 |  | 0.125 | 0.25 | 1 | 8 | 196
3:51:28 PM | 0.17 | 198 | 199 |  | 0.25 | 0.125 | 2 | 8 | 198
3:51:28 PM | 0.26 | 198 | 198 |  | 0.25 | 0
3:51:28 PM | 0.36 | 198 | 200 |  | 0.25 | 0.25 | Pintle Average
3:51:28 PM | 0.48 | 198 | 200 |  | 0.25 | 0.25 | 0.2462871287
3:51:28 PM | 0.56 | 198 | 199 |  | 0.25 | 0.125 | Annulus Average
3:51:28 PM | 0.65 | 197 | 200 |  | 0.125 | 0.25 | 19.17225086
3:51:28 PM | 0.80 | 198 | 199 |  | 0.25 | 0.125
3:51:29 PM | 0.86 | 197 | 200 |  | 0.125 | 0.25
3:51:29 PM | 0.96 | 199 | 199 |  | 0.375 | 0.125
3:51:29 PM | 1.06 | 198 | 199 |  | 0.25 | 0.125
3:51:29 PM | 1.16 | 198 | 199 |  | 0.25 | 0.125
3:51:29 PM | 1.26 | 197 | 199 |  | 0.125 | 0.125
3:51:29 PM | 1.36 | 198 | 199 |  | 0.25 | 0.125
3:51:29 PM | 1.46 | 198 | 199 |  | 0.25 | 0.125
3:51:29 PM | 1.55 | 197 | 199 |  | 0.125 | 0.125
3:51:29 PM | 1.66 | 198 | 199 |  | 0.25 | 0.125
3:51:29 PM | 1.76 | 198 | 200 |  | 0.25 | 0.25
3:51:30 PM | 1.86 | 198 | 199 |  | 0.25 | 0.125
3:51:30 PM | 1.96 | 198 | 200 |  | 0.25 | 0.25
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

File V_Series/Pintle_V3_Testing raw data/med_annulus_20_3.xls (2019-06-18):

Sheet: Analysis
timestamp | timer | pressure_1 | pressure_2 | pressure_2 | PT1 | PT2 | Transducer | Slope | Intercept
3:53:36 PM | 0.05 | 198 | 200 |  | 0.25 | 0.25 | 1 | 8 | 196
3:53:36 PM | 0.18 | 197 | 200 |  | 0.125 | 0.25 | 2 | 8 | 198
3:53:36 PM | 0.25 | 198 | 199 |  | 0.25 | 0.125
3:53:36 PM | 0.36 | 198 | 200 |  | 0.25 | 0.25 | Pintle Average
3:53:36 PM | 0.49 | 197 | 200 |  | 0.125 | 0.25 | 0.2735148515
3:53:36 PM | 0.56 | 197 | 199 |  | 0.125 | 0.125 | Annulus Average
3:53:36 PM | 0.66 | 197 | 200 |  | 0.125 | 0.25 | 18.9469697
3:53:37 PM | 0.75 | 197 | 198 |  | 0.125 | 0
3:53:37 PM | 0.86 | 197 | 199 |  | 0.125 | 0.125
3:53:37 PM | 0.96 | 197 | 199 |  | 0.125 | 0.125
3:53:37 PM | 1.06 | 197 | 199 |  | 0.125 | 0.125
3:53:37 PM | 1.16 | 198 | 200 |  | 0.25 | 0.25
3:53:37 PM | 1.25 | 197 | 199 |  | 0.125 | 0.125
3:53:37 PM | 1.36 | 197 | 199 |  | 0.125 | 0.125
3:53:37 PM | 1.45 | 198 | 199 |  | 0.25 | 0.125
3:53:37 PM | 1.56 | 196 | 200 |  | 0 | 0.25
3:53:37 PM | 1.66 | 198 | 198 |  | 0.25 | 0
3:53:38 PM | 1.77 | 198 | 199 |  | 0.25 | 0.125
3:53:38 PM | 1.86 | 197 | 199 |  | 0.125 | 0.125
3:53:38 PM | 1.95 | 198 | 200 |  | 0.25 | 0.25
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

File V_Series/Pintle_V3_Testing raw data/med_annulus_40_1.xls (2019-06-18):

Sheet: Analysis
timestamp | timer | pressure_1 | pressure_2 | pressure_2 | PT1 | PT2 | Transducer | Slope | Intercept
3:41:27 PM | 0.06 | 197 | 200 |  | 0.125 | 0.25 | 1 | 8 | 196
3:41:27 PM | 0.18 | 198 | 199 |  | 0.25 | 0.125 | 2 | 8 | 198
3:41:27 PM | 0.25 | 200 | 202 |  | 0.5 | 0.5
3:41:27 PM | 0.36 | 198 | 200 |  | 0.25 | 0.25 | Pintle Average
3:41:27 PM | 0.49 | 197 | 200 |  | 0.125 | 0.25 | 0.2920792079
3:41:27 PM | 0.56 | 197 | 199 |  | 0.125 | 0.125 | Annulus Average
3:41:27 PM | 0.66 | 197 | 200 |  | 0.125 | 0.25 | 25.88481675
3:41:28 PM | 0.81 | 198 | 201 |  | 0.25 | 0.375
3:41:28 PM | 0.86 | 198 | 200 |  | 0.25 | 0.25
3:41:28 PM | 0.95 | 198 | 200 |  | 0.25 | 0.25
3:41:28 PM | 1.06 | 198 | 199 |  | 0.25 | 0.125
3:41:28 PM | 1.16 | 197 | 200 |  | 0.125 | 0.25
3:41:28 PM | 1.26 | 198 | 201 |  | 0.25 | 0.375
3:41:28 PM | 1.36 | 198 | 201 |  | 0.25 | 0.375
3:41:28 PM | 1.45 | 198 | 200 |  | 0.25 | 0.25
3:41:28 PM | 1.56 | 197 | 200 |  | 0.125 | 0.25
3:41:28 PM | 1.66 | 198 | 200 |  | 0.25 | 0.25
3:41:29 PM | 1.76 | 197 | 199 |  | 0.125 | 0.125
3:41:29 PM | 1.86 | 197 | 200 |  | 0.125 | 0.25
3:41:29 PM | 1.96 | 197 | 200 |  | 0.125 | 0.25
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

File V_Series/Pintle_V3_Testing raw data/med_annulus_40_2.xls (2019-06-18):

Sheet: Analysis
timestamp | timer | pressure_1 | pressure_2 | pressure_2 | PT1 | PT2 | Transducer | Slope | Intercept
3:44:24 PM | 0.06 | 197 | 200 |  | 0.125 | 0.25 | 1 | 8 | 196
3:44:24 PM | 0.17 | 198 | 199 |  | 0.25 | 0.125 | 2 | 8 | 198
3:44:25 PM | 0.26 | 198 | 199 |  | 0.25 | 0.125
3:44:25 PM | 0.36 | 197 | 199 |  | 0.125 | 0.125 | Pintle Average
3:44:25 PM | 0.48 | 197 | 200 |  | 0.125 | 0.25 | 0.2821782178
3:44:25 PM | 0.56 | 197 | 200 |  | 0.125 | 0.25 | Annulus Average
3:44:25 PM | 0.66 | 198 | 198 |  | 0.25 | 0 | 23.86647727
3:44:25 PM | 0.80 | 198 | 200 |  | 0.25 | 0.25
3:44:25 PM | 0.86 | 199 | 200 |  | 0.375 | 0.25
3:44:25 PM | 0.96 | 198 | 199 |  | 0.25 | 0.125
3:44:25 PM | 1.06 | 198 | 199 |  | 0.25 | 0.125
3:44:25 PM | 1.16 | 197 | 198 |  | 0.125 | 0
3:44:26 PM | 1.26 | 196 | 200 |  | 0 | 0.25
3:44:26 PM | 1.36 | 199 | 200 |  | 0.375 | 0.25
3:44:26 PM | 1.45 | 198 | 200 |  | 0.25 | 0.25
3:44:26 PM | 1.56 | 197 | 199 |  | 0.125 | 0.125
3:44:26 PM | 1.66 | 197 | 200 |  | 0.125 | 0.25
3:44:26 PM | 1.76 | 198 | 199 |  | 0.25 | 0.125
3:44:26 PM | 1.86 | 197 | 198 |  | 0.125 | 0
3:44:26 PM | 1.96 | 197 | 200 |  | 0.125 | 0.25
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

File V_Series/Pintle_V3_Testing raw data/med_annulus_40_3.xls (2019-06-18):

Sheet: Analysis
timestamp | timer | pressure_1 | pressure_2 | pressure_2 | PT1 | PT2 | Transducer | Slope | Intercept
3:49:22 PM | 0.05 | 198 | 198 |  | 0.25 | 0 | 1 | 8 | 196
3:49:22 PM | 0.17 | 198 | 199 |  | 0.25 | 0.125 | 2 | 8 | 198
3:49:22 PM | 0.25 | 198 | 199 |  | 0.25 | 0.125
3:49:22 PM | 0.35 | 197 | 199 |  | 0.125 | 0.125 | Pintle Average
3:49:22 PM | 0.48 | 197 | 198 |  | 0.125 | 0 | 0.2673267327
3:49:22 PM | 0.55 | 198 | 199 |  | 0.25 | 0.125 | Annulus Average
3:49:22 PM | 0.65 | 198 | 199 |  | 0.25 | 0.125 | 16.15422886
3:49:23 PM | 0.80 | 197 | 199 |  | 0.125 | 0.125
3:49:23 PM | 0.85 | 198 | 199 |  | 0.25 | 0.125
3:49:23 PM | 0.95 | 198 | 200 |  | 0.25 | 0.25
3:49:23 PM | 1.05 | 198 | 199 |  | 0.25 | 0.125
3:49:23 PM | 1.15 | 198 | 200 |  | 0.25 | 0.25
3:49:23 PM | 1.25 | 197 | 199 |  | 0.125 | 0.125
3:49:23 PM | 1.35 | 197 | 199 |  | 0.125 | 0.125
3:49:23 PM | 1.45 | 197 | 199 |  | 0.125 | 0.125
3:49:23 PM | 1.55 | 197 | 199 |  | 0.125 | 0.125
3:49:23 PM | 1.65 | 198 | 199 |  | 0.25 | 0.125
3:49:23 PM | 1.75 | 197 | 199 |  | 0.125 | 0.125
3:49:24 PM | 1.85 | 197 | 199 |  | 0.125 | 0.125
3:49:24 PM | 1.95 | 198 | 198 |  | 0.25 | 0
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

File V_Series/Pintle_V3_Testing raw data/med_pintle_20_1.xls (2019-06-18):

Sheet: Analysis
timestamp | timer | pressure_1 | pressure_2 | pressure_2 | PT1 | PT2 | Transducer | Slope | Intercept
4:01:36 PM | 0.05 | 195 | 199 |  | -0.125 | 0.125 | 1 | 8 | 196
4:01:36 PM | 0.17 | 195 | 199 |  | -0.125 | 0.125 | 2 | 8 | 198
4:01:36 PM | 0.25 | 195 | 199 |  | -0.125 | 0.125
4:01:36 PM | 0.35 | 195 | 199 |  | -0.125 | 0.125 | Pintle Average
4:01:36 PM | 0.49 | 195 | 200 |  | -0.125 | 0.25 | 14.06104651
4:01:36 PM | 0.55 | 195 | 200 |  | -0.125 | 0.25 | Annulus Average
4:01:36 PM | 0.65 | 194 | 199 |  | -0.25 | 0.125 | 0.07564575646
4:01:36 PM | 0.75 | 195 | 200 |  | -0.125 | 0.25
4:01:36 PM | 0.85 | 195 | 199 |  | -0.125 | 0.125
4:01:36 PM | 0.95 | 195 | 199 |  | -0.125 | 0.125
4:01:37 PM | 1.05 | 195 | 199 |  | -0.125 | 0.125
4:01:37 PM | 1.15 | 194 | 199 |  | -0.25 | 0.125
4:01:37 PM | 1.25 | 195 | 199 |  | -0.125 | 0.125
4:01:37 PM | 1.35 | 195 | 198 |  | -0.125 | 0
4:01:37 PM | 1.45 | 195 | 199 |  | -0.125 | 0.125
4:01:37 PM | 1.55 | 196 | 200 |  | 0 | 0.25
4:01:37 PM | 1.65 | 195 | 200 |  | -0.125 | 0.25
4:01:37 PM | 1.76 | 195 | 199 |  | -0.125 | 0.125
4:01:37 PM | 1.85 | 194 | 200 |  | -0.25 | 0.25
4:01:37 PM | 1.95 | 195 | 199 |  | -0.125 | 0.125
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

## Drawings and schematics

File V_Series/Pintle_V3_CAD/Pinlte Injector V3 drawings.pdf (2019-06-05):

15

# 32 " THRU

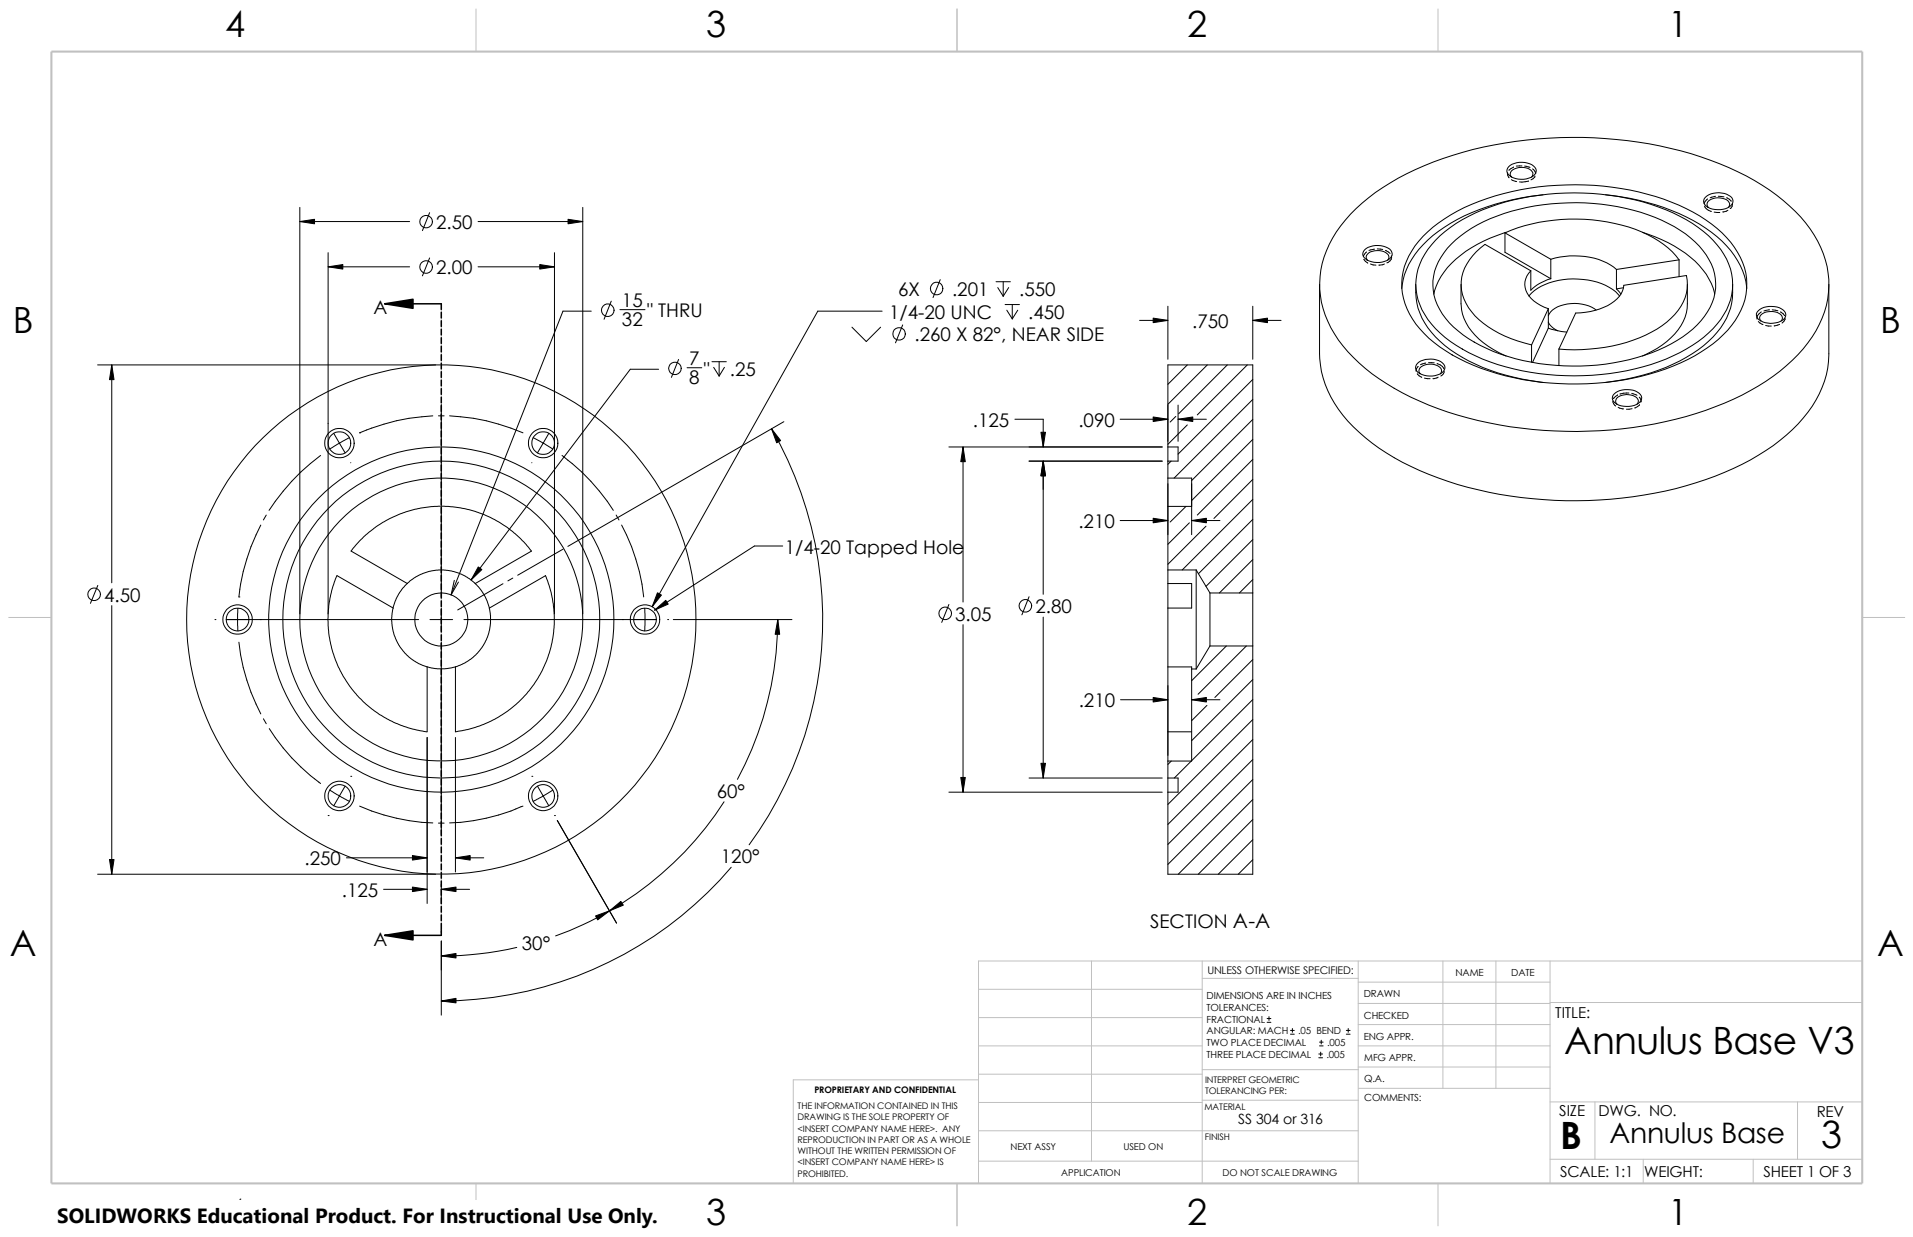
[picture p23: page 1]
1/4-20 Tapped Hole; 1/4-20 UNC; .260 X 82°, NEAR SIDE; COMMENTS:; SECTION A-A

UNLESS OTHERWISE SPECIFIED: | | NAME | DATE

DIMENSIONS ARE IN INCHES TOLERANCES: FRACTIONAL ANGULAR: MACH .05 BEND TWO PLACE DECIMAL .005 THREE PLACE DECIMAL .005 | DRAWN

CHECKED | | | TITLE: Annulus Base V3

ENG APPR.
MFG APPR.

INTERPRET GEOMETRIC TOLERANCING PER: | Q.A.
MATERIAL SS 304 or 316 | | SIZE B | DWG. NO. Annulus Base | REV 3

PROPRIETARY AND CONFIDENTIAL
THE INFORMATION CONTAINED IN THIS
DRAWING IS THE SOLE PROPERTY OF
<INSERT COMPANY NAME HERE>. ANY
REPRODUCTION IN PART OR AS A WHOLE
WITHOUT THE WRITTEN PERMISSION OF
<INSERT COMPANY NAME HERE> IS
PROHIBITED.

NEXT ASSY | USED ON | FINISH

APPLICATION | DO NOT SCALE DRAWING | | SCALE: 1:1 | WEIGHT: | SHEET 1 OF 3

SOLIDWORKS Educational Product. For Instructional Use Only.

2.250
B B

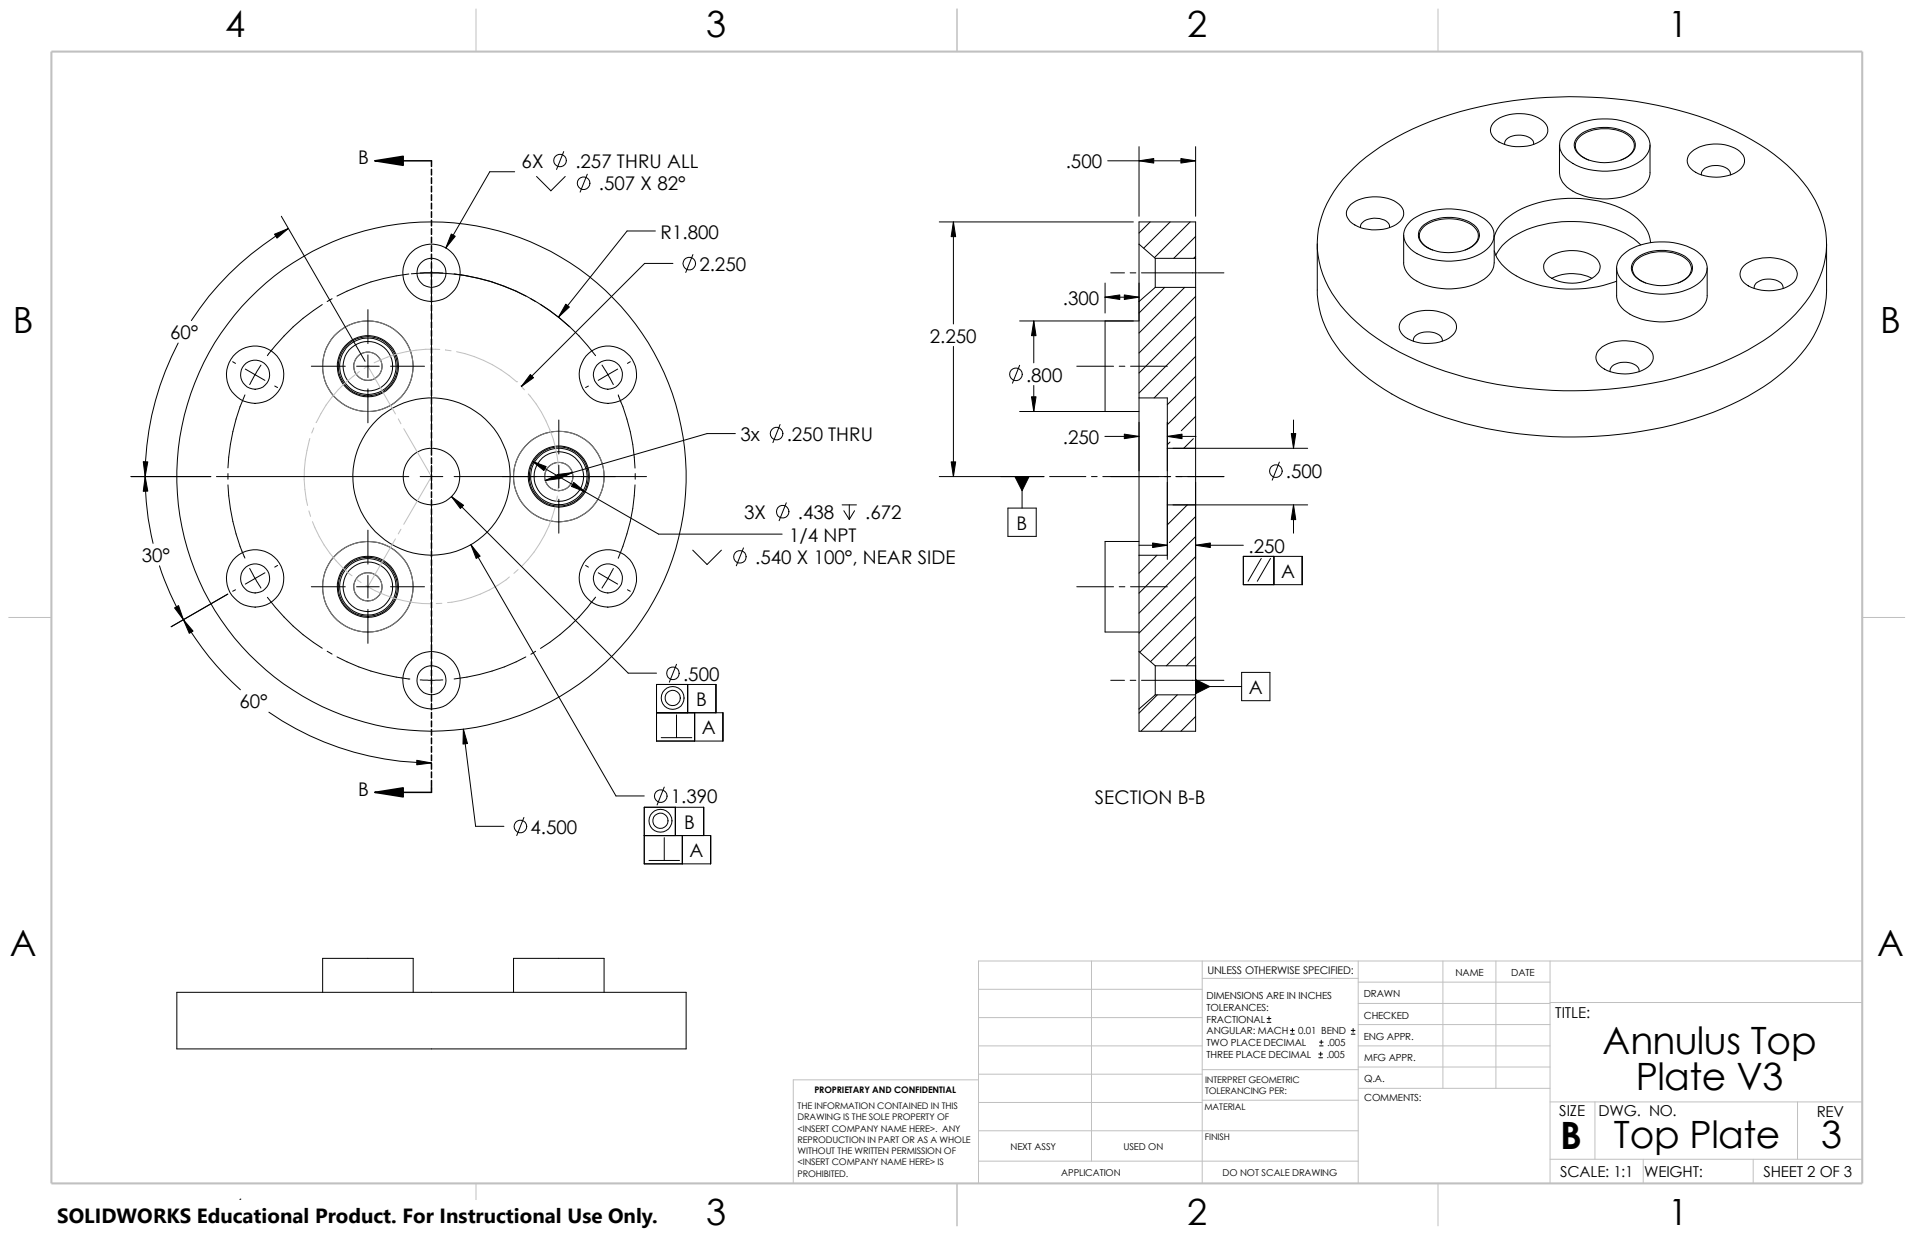
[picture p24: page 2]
Top Plate; SHEET 2 OF 3; DWG. NO.; REV; SIZE; COMMENTS:; MATERIAL; SECTION B-B; .257 THRU ALL; 1/4 NPT .540 X 100°, NEAR SIDE; 3x .250 THRU

UNLESS OTHERWISE SPECIFIED: | | NAME | DATE

DIMENSIONS ARE IN INCHES TOLERANCES: FRACTIONAL ANGULAR: MACH 0.01 BEND TWO PLACE DECIMAL .005 THREE PLACE DECIMAL .005 | DRAWN

CHECKED | | | TITLE: Annulus Top Plate V3

ENG APPR.
MFG APPR.

INTERPRET GEOMETRIC TOLERANCING PER: | Q.A.

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

B B

.438 .768

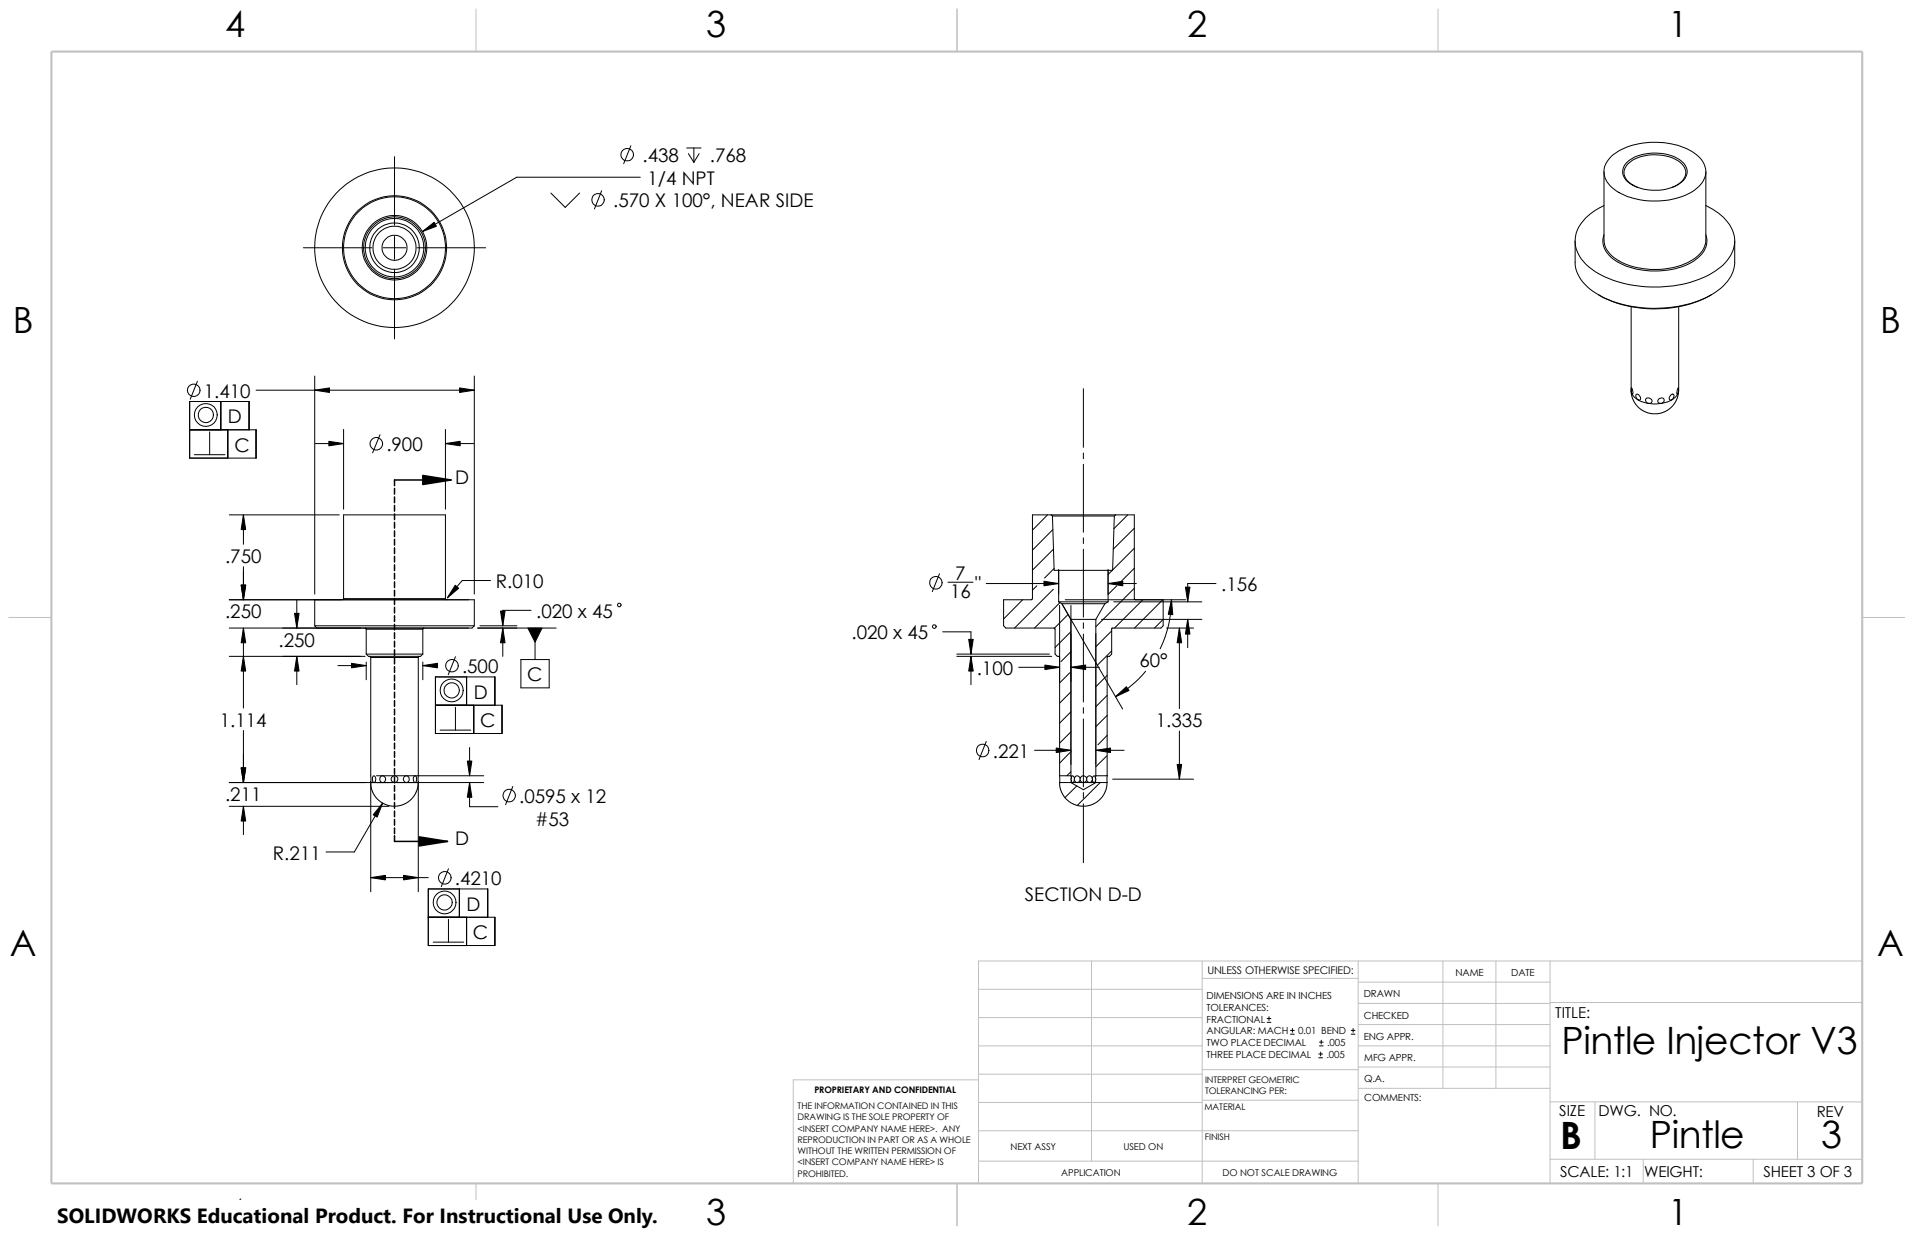
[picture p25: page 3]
Pintle; SHEET 3 OF 3; DWG. NO.; REV; SIZE; COMMENTS:; MATERIAL; SECTION D-D; 1/4 NPT .570 X 100°, NEAR SIDE

UNLESS OTHERWISE SPECIFIED: | | NAME | DATE

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

CHECKED | | | TITLE: Pintle Injector V3

ENG APPR.
MFG APPR.

INTERPRET GEOMETRIC TOLERANCING PER: | Q.A.

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

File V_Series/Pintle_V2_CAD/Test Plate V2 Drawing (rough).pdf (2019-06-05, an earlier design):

B B

2

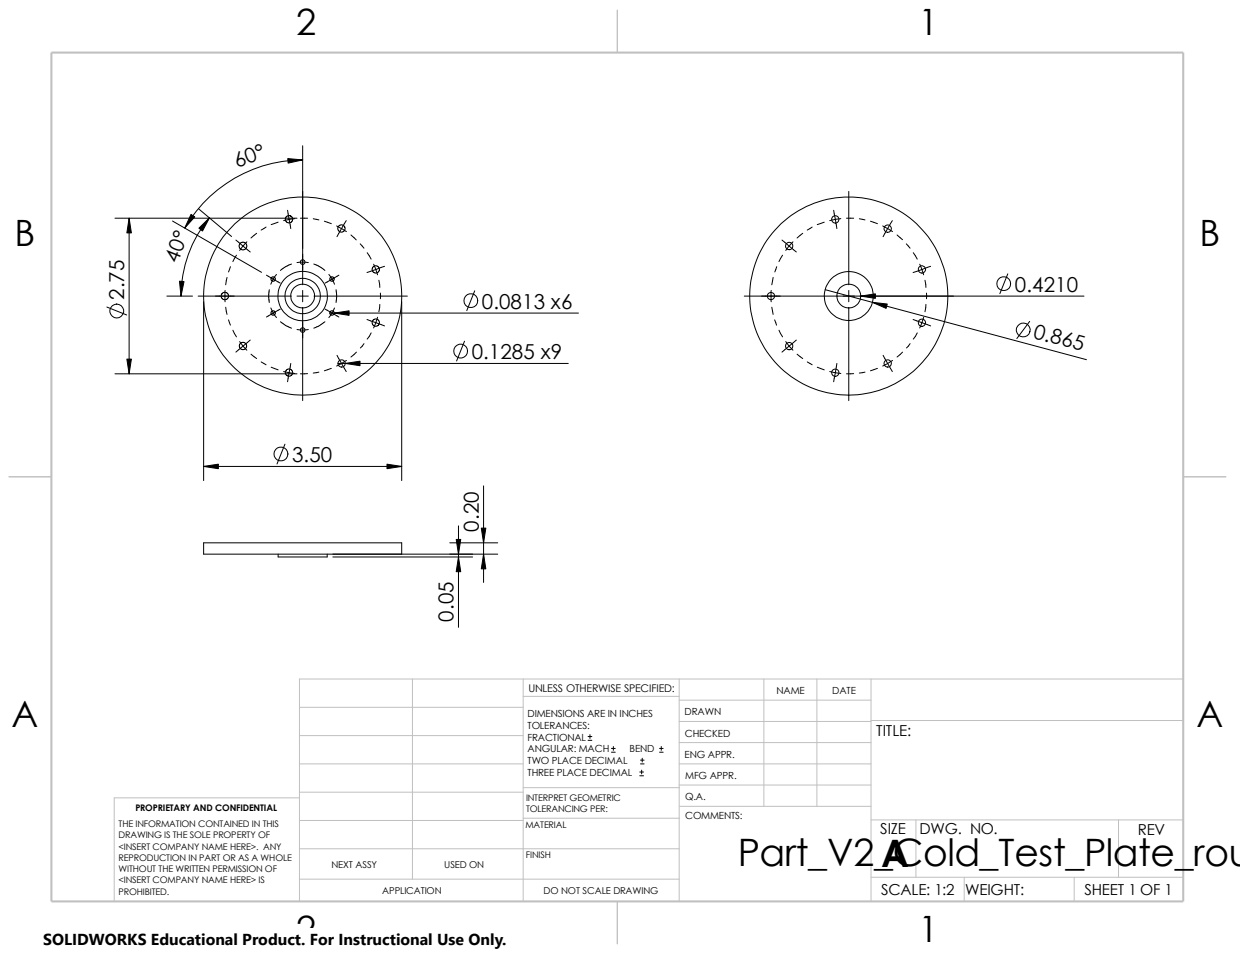
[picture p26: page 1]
Part_V2_Cold_Test_Plate_rough A; COMMENTS:; INTERPRET GEOMETRIC; PROPRIETARY AND CONFIDENTIAL; TOLERANCING PER:; PROHIBITED.

UNLESS OTHERWISE SPECIFIED: | | NAME | DATE

DIMENSIONS ARE IN INCHES TOLERANCES: FRACTIONAL ANGULAR: MACH BEND TWO PLACE DECIMAL THREE PLACE DECIMAL | DRAWN

CHECKED | | | TITLE:

ENG APPR.
MFG APPR.

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

MATERIAL | | SIZE | DWG. NO. | REV

NEXT ASSY | USED ON | FINISH
APPLICATION | DO NOT SCALE DRAWING | | SCALE: 1:2 | WEIGHT: | SHEET 1 OF 1

SOLIDWORKS Educational Product. For Instructional Use Only.

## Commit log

2019-06-05 First commit, moving files from the Test Stand repo to their new home
    [0 psi calibration 2.xls, 0 psi calibration.xls, 0 psi calibration.xlsx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]
2019-06-18 updates to the Pintle Design Documentation and some reorganization
    [0 psi calibration 2.xls, 0 psi calibration.xls, 0 psi calibration.xlsx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]
2019-06-30 updates to pintle design documentation
    [00 Pintle Data Analysis 01-26-2019.xlsx, Data Analysis Summary.xlsx]
2020-12-22 Add files via upload
    Set up flow simulation in CAD and added lids.
    [Assembly_Pintle_V3.SLDASM]
2020-12-31 Clean Up
    Added labels to dimensions in V3 Cad.
    [Assembly_Pintle_V3.SLDASM, LID1.SLDPRT, LID2.SLDPRT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]
2020-12-31 Tweaked Sim
    [Assembly_Pintle_V3.SLDASM, global_parameters.txt]
2021-05-12 made parasolid for STARCCM
    [Part_V3_Pintle.x_t]
